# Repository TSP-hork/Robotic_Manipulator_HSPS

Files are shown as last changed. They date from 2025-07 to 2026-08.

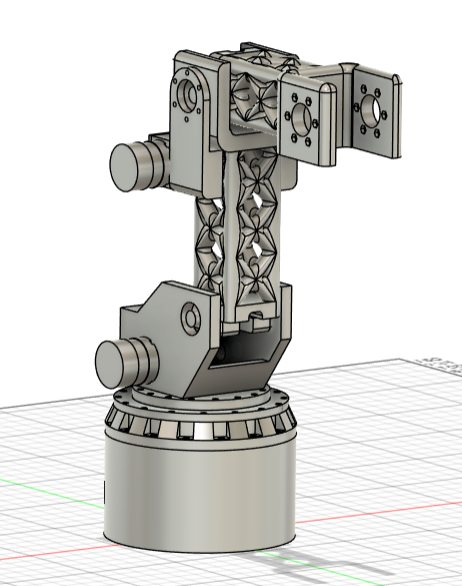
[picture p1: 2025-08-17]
cad/docs/CAD_views/Atlas_v1_pict_3.png

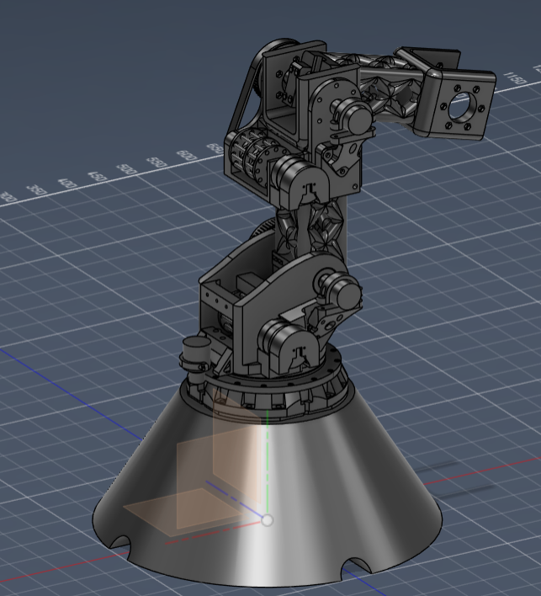
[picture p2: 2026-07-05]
cad/docs/CAD_views/Atlas_v2_pict_1.png

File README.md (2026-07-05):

# Robotic_Manipulator_HSPS

This repository is dedicated to the development of a High-Performance, Open-Source Robotic Manipulator based on a Hot-Swappable Part System (HSPS).

## Hot... what?

Yes, "Hot-Swappable" sounds strange for a robotic arm. Controlling a robot like this usually requires deep programming skills and a complex system understanding, making most designs rigid and hard to modify. My goal is to make it easier. And no, this is not a toy for grabbing cubes.

## What does "not a toy" mean?

A toy can grab something. A toy can rotate. This robot is designed to be a true industrial tool. It's designed to be precise and powerful enough to mill its own parts from aluminum, to weld, or to perform any task you can imagine.

The core idea is simple: This project provides a blueprint for anyone with common tools (like a 3D printer) and dedication to build an instrument capable of creating almost anything.

## How "good" is this cheap thing?

You might be thinking: "Okay, so you're making a cheap little arm and believe it can compete with a true, big, metal one? That's nonsense." And you are half right. This robot can't mill hardened steel or titanium. But does it need to?

What we all really need are strong, precise parts. We can't 3D-print metal, but this robot is designed to be precise enough to **mill aluminum**. This means you can use the first plastic robot to create the parts for its much stronger, metal successor. Sounds more realistic now, doesn't it?

But what about the "brains"? I've got you covered there too. This robot is being designed to run its control loop at **50 kHz**. This means it can react to a command in **20 microseconds** - the time from your signal to a change in the motor's current. And yes, it will work with almost any motor you want.

## Nice to meet you

I bet this sounds interesting. I just want to say hello, and I'm glad to see you here. This project started on May 27, 2025, and my goal is to build the first working prototype by next summer.

Maybe I'll make it, maybe I won't, but we'll find that out together. For now, you can find me here every Saturday. Let's get started!

## 05.07.26 Update "After a year"

Yeah, looking back, I wasn't sure what I was getting into at the start. I honestly thought I'd just tinker for a month and drop it, but here we are. Let's see what we've achieved!

I have finished the mechanics (I'd say they are 99% done). I also developed a 1kW motor driver—you can grab the Gerbers and order the boards for yourself(please note the non-commercial license below! sry for that). I've tested it and it works great, though I will personally be running it at 200W for this robot. I also wrote the FOC algorithm to control the motors.

I'll be continuing this journey, and I might change the name of the project soon. I really was here almost every Saturday (well, maybe not every single one, but I tried!).

A huge thank you to the two guys who starred my repo—it means a lot! I will keep going, we can do this! <Have a good day!> :>

## ⚖️ License

This project uses a **Dual-Licensing** model to protect both the software and the hardware designs.

*   **Software / Firmware:** All source code in this repository is licensed under the **GNU General Public License v3.0 (GPLv3)**. See the `LICENSE` file in the root directory for details.
*   **Hardware Designs:** All hardware files (Gerbers, Schematics, BOM, Pick and Place files, and 3D CAD models) located in the hardware/cad directories are licensed under the **Creative Commons Attribution-NonCommercial 4.0 International (CC BY-NC 4.0)** license. See the `LICENSE_HARDWARE.md` file for details.

**What this means for you:**
You are completely free to use, modify, and build the software and hardware for your own personal, educational, or hobby projects. However, **you may not use the hardware files for commercial purposes** (e.g., you cannot mass-produce the PCBs to sell them) without explicit permission.

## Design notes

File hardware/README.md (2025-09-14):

This document outlines the core hardware architecture and key component decisions for the project.
*If I write it 100 times, I won't forget it ~~(but that might not be true)~~.*

## 2025-08-14: Hardware Architecture Decisions

* **System Architecture:** The core control system will be a **unified motherboard**. This board will house the primary MCandFPGA, and provide standardized **blade ports** for connecting to the external **power stages** and other peripherals.

* **Performance Target:** The architecture is designed with a future performance target of **200+ kHz** for the core control loop, ensuring a high ceiling for future optimizations.

* **Core Philosophy:** A hybrid **MC + FPGA** approach. The microcontroller acts as the "smart" commander for high-level tasks, while the FPGA serves as the "fast and strong" hardware accelerator for real-time control loops.

* **Microcontroller (MC):** STM32H7A3. Chosen for its powerful Cortex-M7 core, large SRAM, and sufficient processing power to handle kinematics and trajectory planning without becoming a bottleneck.

* **FPGA:** Lattice ECP5, LFE5U-45F. This chip is selected for its excellent balance of price and performance. With **44K LUTs**, it has more than enough resources to implement six parallel, **hardware-accelerated FOC cores**, leaving significant potential for future features.

* **power on mainboard** POWER on board going from board with stabilizators, filters and maybe little MC who just watch for safe all board and stop the current if he is very high. And in future i want only 48 V for step down on blades(if that needs) and mother board.

* **power on input board** POWER on this board comming from any POWER supply who can give 300 W +- or any other count of W 

* **Input board** Thats board is not very smart. with simple MC and passive components who stabilize and filter input POWER.
Is step up or step down supply and send it to main board on two wire VCC and GND. Mb in very far future i make uart for errors from this stage but i think one LED is over and enough.

* **outcontrol blade** is technologist in my system, he can be very smart or very ..khm he can be SD and just talking simple commands, or its can be computer with cam with AI who can talk with this world of any protocol, but with arm he talking on speed of electricity (i just like how its sounds).

* **between FPGA and blade** While i dont forgeted, FPGA not strong enough for control blades and he need a help. For this on road from his leg to blade we need dif converter (working on RS-422) who can send his messages without noices to gate driver. This guy can control strong MOSFETs very fast and he is cheap we accept him to our team. 

## 2025-08-24: the architecture of my electronics

* **main date** so today i start develop my electronics, and start print mechanic. I add new directory to docs for top_sheet. i think i need develop electronics parralel work cuz develop electronics need more time for think than act. Have a good last days of summer -^-

## 2025-09-02: Structure update !!

```
hardware/
├── libraries/
│   ├── symbols/
│   │   └── My_Symbols.SchLib
│   ├── footprints/
│   │   └── My_Footprints.PcbLib
│   └── 3d_models/
│       ├── SP3485.step
│       └── LFE5U-45F.step
├── projects/
│   ├── Axis_Channel_Blade/
│   │   ├── Axis_Channel.PrjPcb
│   │   ├── Axis_Channel.SchDoc
│   │   └── Axis_Channel.PcbDoc
│   ├── Motherboard/
│   │   ├── Motherboard.PrjPcb
│   │   ├── ...
│   └── Input_Board/
│       ├── Input_Board.PrjPcb
│       ├── ...
├── production/
│   ├── Axis_Channel_Blade/
│   │   ├── rev1.0/
│   │   │   ├── gerber/
│   │   │   ├── bom/
│   │   │   └── pick_and_place/
│   │   └── rev1.1/
│   │       ├── ...
│   └── Motherboard/
│       └── rev1.0/
│           ├── ...
└── datasheets/
    ├── IC/
    │   ├── LFE5U-45F.pdf
    │   └── SN65HVD75.pdf
    └── connectors/
        └── Samtec_QSE_series.pdf
```

* **start develop POWER blade** With structure i start to develop blade and for today maked arhitecture of blade

## 2025-09-09: for future :>

* **INA190** amplifier for function hot swap motors. we can change V/V using logic signals from stm. Or we can just use better ADC and place low shunt (1 M ohm) for any current ~~(max 50A)~~ but its expensive.

* **Comment** : for version 1.0, I don't do hot swapping because if I don't build this robot or it doesn't work with my motors, it won't work with any motors, and it doesn't make sense anyway :/ 
**But if it works, I'll definitely make this feature the first one.**

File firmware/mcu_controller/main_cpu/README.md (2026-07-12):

# Main CPU Firmware Architecture

## Overview

This firmware runs on the STM32H7 (280 MHz Cortex-M7) and implements the
control algorithms for a robotic manipulator. The architecture is designed
around three principles:

1. **Portability** — algorithms are hardware-independent and can run on any MCU
2. **Extensibility** — new features are added without modifying existing code
3. **Determinism** — zero runtime overhead from the architecture itself

The system is split into layers. Each layer has exactly one responsibility
and exactly one reason to change.

```
┌─────────────────────────────────────────────┐
│  logic/         Pure algorithms (C/C++)     │ ← portable
│  utility/       Reusable building blocks    │ ← portable (planned)
│  abstract/      Hardware contract (C)       │ ← stable, rarely changes
│  driver/        Chip-specific code (C/ASM)  │ ← replaced per platform
└─────────────────────────────────────────────┘
```

The final system will implement a real-time cascade:

```
Trajectory (100 Hz)                             ← logic done (not integrated)
    → Kinematics (100 Hz)                       ← positioner done, wrist skeleton
        → Servo loop (1 kHz)                    ← logic done (not integrated)
            → FOC current loop (20 kHz)         ← IMPLEMENTED
                → PWM output (via FPGA)         ← IMPLEMENTED
```

Each level only talks to its neighbors. FOC does not know about kinematics.
Kinematics does not know about PWM registers.

## Current State

The FOC current control layer is fully operational on hardware. The higher
cascade levels are being built bottom-up as portable, desktop-testable logic:
the servo loop, the trajectory planner, and the 3-axis kinematics positioner
are written and validated but not yet wired into the running cascade. The wrist
(orientation) kinematics, runtime state machine, and safety guardian remain to
be done.

**What works today:**
- Field-Oriented Control with Clarke/Park transforms
- PI current regulators (d-axis and q-axis)
- Space-Vector PWM modulation with min-max injection
- Full-duplex SPI data exchange with the FPGA at 20 kHz
- Multiple compile-time run modes for calibration and testing
- 280 MHz clock configuration (HSE bypass + PLL)
- DMA-driven SPI slave with EXTI interrupt

**Logic written & validated (portable, desktop-tested, not yet integrated):**
- Position/velocity servo loop with feed-forward
- Jerk-limited S-curve trajectory planning + multi-axis interpolator
- Forward kinematics (general, any axis count) + 3-axis closed-form inverse
- Geometric Jacobian and manipulability (singularity) measure
- Software FPU sin/cos provider (swappable backend)

**What is planned:**
- Servo loop compile-time extensions (damping, friction, …)
- Wrist / orientation inverse kinematics (4/5/6-axis, skeleton in place)
- Cascade integration (trajectory → kinematics → servo → FOC)
- State machine and operating modes
- Technologist module communication protocol
- Safety guardian (last barrier before hardware)
- Hardware CORDIC acceleration for sin/cos (needs a CORDIC-equipped MCU)

## Directory Structure

```
main_cpu/
│
├── 1_logic/                            # Pure algorithms — PORTABLE
│   ├── foc.c                           # FOC: Clarke, Park, PI, inv. Park, SVPWM
│   ├── foc.h                           # FOC interface and output structures
│   └── pid.h                           # PI controller (static inline)
│   │
│   ├── 0_foc/                          # (planned) FOC refactored into C++ class
│   │   ├── foc.hpp
│   │   ├── clarke_park.hpp
│   │   └── svpwm.hpp
│   │
│   ├── 1_servo/                        # Position/velocity servo — IMPLEMENTED
│   │   ├── servo.c / .h                # Cascade P-pos + PI-vel, with feed-forward
│   │   └── extensions/                 # (planned) Servo loop extensions (∞)
│   │       ├── damping/
│   │       │   └── damping.hpp
│   │       ├── friction/
│   │       │   └── friction.hpp
│   │       └── .../
│   │
│   ├── 2_kinematics/                   # Forward/inverse kinematics — IMPLEMENTED (logic only)
│   │   ├── kinematics.c / .h           # Façade + core: general FK, IK dispatch, Jacobian
│   │   ├── seg_position3.c / .h        # Closed-form 3-axis positioner (base + shoulder + elbow)
│   │   └── seg_wrist3.c / .h           # (skeleton) 1/2/3-DOF wrist for 4/5/6-axis arms
│   │
│   ├── 3_trajectory/                   # Path planning — IMPLEMENTED (logic only)
│   │   ├── s_curve.c / .h              # Jerk-limited 7-segment S-curve profile
│   │   └── interpolator.c / .h         # Multi-axis sync + waypoint sequencing
│   │
│   ├── 4_runtime/                      # (planned) System orchestration
│   │   ├── state_machine.cpp
│   │   ├── homing.cpp
│   │   ├── protocol/                   # Technologist module communication
│   │   │   ├── packet.cpp
│   │   │   ├── commands.cpp
│   │   │   └── feedback.cpp
│   │   └── modes/                      # Special operating modes (∞)
│   │       └── resonance_scan/
│   │
│   └── safety/                         # (planned) Safety — ALWAYS ON
│       ├── guardian.cpp
│       └── watchdog.cpp
│
├── 2_utility/                                # (planned) Reusable building blocks
│   ├── math/
│   │   ├── matrix/
│   │   ├── quaternion/
│   │   └── spline/
│   ├── control/
│   │   ├── pid/
│   │   └── filters/
│   ├── signal/
│   │   └── dsp/
│   └── utils/
│       ├── ring_buffer/
│       └── crc/
│
├── 3_abstract/                         # Hardware contract — STABLE
│   └── types.h                         # Shared structures (SPI packets, phase_t)
│   └── hw_contract.h                   # (planned) Documents required HW functions
│
├── 4_driver/stm32h7a3zit6_Q/          # Chip-specific — REPLACEABLE
│   ├── config.h                        # Run mode, motor params, ADC calibration
│   ├── hw_impl.h                       # Inline HW functions (the bridge)
│   ├── hw_binding.c                    # Peripheral init orchestration
│   ├── isr.c                           # EXTI4 handler (FOC pipeline runs here)
│   ├── spi.c                           # SPI3 slave + DMA configuration
│   ├── spi.h
│   ├── rcc.c                           # Clock tree (280 MHz from HSE + PLL)
│   ├── rcc.h
│   ├── gpio.c                          # Diagnostic LED pins
│   ├── gpio.h
│   ├── tim.c                           # TIM6 microsecond timer
│   ├── tim.h
│   └── startup/
│       ├── STM32H7A3ZITXQ_FLASH.ld    # Linker script
│       └── startup_stm32h7a3xx.s       # Vector table + reset handler
│
├── tests/                              # Desktop unit tests (NOT built into firmware)
│   └── test_trajectory.c               # Host-compiled tests for 3_trajectory/
├── main.cpp                            # Entry point + configuration
├── CMakeLists.txt                      # Build system (ARM cross-compilation)
└── Makefile                            # Convenience wrapper (config/build/flash)
```

Items marked **(planned)** do not exist yet. They represent the target
architecture that will be built incrementally.

---

## Layer Rules

### logic/ — Pure Algorithms

**Language:** C today, C++ when servo layer is added

**Rules:**
- NEVER includes chip-specific headers directly
- NEVER accesses hardware registers
- ONLY calls functions from `hw_impl.h` and `utility/`
- CAN be compiled and tested on a desktop PC

**Numbering convention:** prefixes `0_`, `1_`, `2_`, `3_`, `4_` indicate the
cascade level. Lower number = faster loop = closer to hardware.

```
0_foc        20 kHz    current control          ← IMPLEMENTED (as foc.c)
1_servo       1 kHz    position/velocity        ← logic done, not integrated
2_kinematics  100 Hz   joint-to-cartesian       ← positioner done, wrist skeleton
3_trajectory  100 Hz   path planning            ← logic done, not integrated
4_runtime     main()   state machine, commands  ← planned
```

### utility/ — Reusable Building Blocks (planned)

**Language:** C or C++

**Rules:**
- Pure math and utilities — no hardware, no state machines
- Each block is self-contained with its own `.h` and `.c`/`.cpp`
- ONLY placed in `utility/` if used by **more than one** module in `logic/`
- If used by only one module — keep it inside that module

**Grouping:**
- `math/` — linear algebra, quaternions, splines
- `control/` — PID, filters, observers
- `signal/` — DSP, FFT, spectral analysis
- `utils/` — ring buffers, CRC, data structures

### abstract/ — Hardware Contract

**Language:** C (with `extern "C"` guards)

**Rules:**
- Contains ONLY header files
- `types.h` defines shared data structures used across all layers
- `hw_contract.h` (planned) documents the functions that `driver/` must implement
- This layer **almost never changes** — it is the stable interface

**Currently implemented:** `types.h` with SPI packet structures (`spi_rx_packet_t`,
`spi_tx_packet_t`, `axis_rx_t`, `axis_tx_t`), FOC types (`phase_t`, `rotor_t`),
and compile-time size assertions.

**`hw_contract.h` will document** the functions that every `driver/xxx/hw_impl.h`
must provide:

```
// hw_contract.h — Every driver/ MUST provide hw_impl.h containing:
//
//   static inline phase_t  hw_read_currents(void);
//   static inline rotor_t  hw_read_rotor(void);
//   static inline void     hw_write_pwm(phase_t duty);
//   static inline void     hw_sincos(float angle, float *s, float *c);
//   static inline void     hw_enable_gate(void);
//   static inline void     hw_disable_gate(void);
//   static inline uint32_t hw_micros(void);
```

### driver/ — Chip-Specific Implementation

**Language:** C + ASM

**Rules:**
- ONLY this layer knows about registers, DMA channels, pin numbers
- Implements all functions listed in `hw_contract.h`
- `hw_impl.h` uses `static inline` — zero overhead, compiler inlines everything
- `vendor/CMSIS/` contains third-party headers — **do not edit**
- When switching MCU, **only this layer is rewritten**

**Currently implemented:**
- `rcc.c` — full clock tree (280 MHz: HSE bypass → PLL → SYSCLK)
- `gpio.c` — diagnostic LED pins (PB0, PE1, PB14)
- `tim.c` — TIM6 as 1 µs free-running timer
- `spi.c` — SPI3 slave with DMA + EXTI4 interrupt on CS line
- `isr.c` — EXTI4 handler running the entire FOC pipeline
- `hw_binding.c` — calls all peripheral inits in correct order
- `hw_impl.h` — SPI buffer accessors (full hw functions are stubs for now)
- `config.h` — motor parameters, run mode selection, calibration constants

---

## How It Works Today

### The Interrupt-Driven FOC Loop

The entire control loop is driven by a single interrupt — EXTI4 on PA4,
triggered by the FPGA's SPI chip-select signal at 20 kHz:

```
FPGA asserts CS (falling edge)
    │
    ▼
EXTI4 ISR: configure DMA, enable SPI3
    │
    ... 256-bit SPI transfer (hardware, no CPU) ...
    │
FPGA releases CS (rising edge)
    │
    ▼
EXTI4 ISR: disable SPI3, then:
    1. Read RX buffer (encoder positions + ADC currents from FPGA)
    2. Run FOC: Clarke → Park → PI → inverse Park → SVPWM
    3. Fill TX buffer (PWM duty commands for FPGA)
    4. Reset SPI3 peripheral for next frame
    5. Return from ISR
    │
    ▼
CPU sleeps (__WFI) until next CS edge
```

No timer interrupts. No polling loops. The FPGA's 20 kHz tick is the sole
timing reference for the MCU.

### SPI Data Exchange

The MCU communicates with the FPGA via a 256-bit (32-byte) full-duplex
SPI frame every 50 µs. Packet structures are defined in `types.h`:

**FPGA → MCU (sensor data):**
```
typedef struct __attribute__((packed)) {
    uint32_t  sync;                     // 0xAA55AA55 — frame validation
    axis_rx_t axis[AXIS_COUNT];         // Per-axis: 2×16-bit ADC + 32-bit encoder
    uint32_t  sequence;                 // FPGA frame counter
} spi_rx_packet_t;
```

**MCU → FPGA (commands):**
```
typedef struct __attribute__((packed)) {
    uint32_t  magic;                    // 0xDEADBEEF — link validation
    axis_tx_t axis[AXIS_COUNT];         // Per-axis: 3×16-bit PWM + 16-bit flags
    uint32_t  status;                   // MCU processed-frame counter
} spi_tx_packet_t;
```

Both packets are exactly 32 bytes. Compile-time `_Static_assert` checks
guarantee size consistency.

### Run Modes

Operating behavior is selected at compile time via `RUN_MODE` in `config.h`.
This avoids runtime branching overhead and allows the compiler to eliminate
dead code entirely.

| Mode | Name | Description |
|---|---|---|
| 0 | Open-loop rotation | Rotating voltage vector, no feedback. ADC test |
| 1 | Encoder test | Motor disabled, encoder readback only |
| 2 | Alignment | Static d-axis vector, captures encoder offset  |
| 3 | Align → FOC | 2s alignment, then closed-loop current control |
| 4 | Full FOC | All axes, production mode (needs outer loop) |

### FOC Pipeline (foc.c)

Executes every 50 µs inside the EXTI4 ISR:

```
Phase currents (ia, ib from FPGA's ADC data)
        │
        ▼
  Clarke Transform
  ia, ib → iα, iβ
        │
        ▼
  Park Transform (using electrical angle from encoder)
  iα, iβ → id, iq
        │
        ▼
  PI Current Regulators (pid.h, static inline)
  id_error → vd    (flux, always targets 0)
  iq_error → vq    (torque, set by outer loop or test constant)
        │
        ▼
  Inverse Park Transform
  vd, vq → vα, vβ
        │
        ▼
  SVPWM Modulator (min-max injection, +15% bus utilization)
  vα, vβ → pwm_a, pwm_b, pwm_c  (0..PWM_PERIOD ticks)
        │
        ▼
  Packed into SPI TX buffer → sent to FPGA on next frame
```

### The Bridge: hw_impl.h

This file connects portable logic to real hardware. Currently it provides
SPI buffer accessors. As the architecture matures, it will contain direct
register access for ADC, PWM, and CORDIC:

```
// Current state: SPI-mediated access to FPGA buffers
static inline volatile spi_rx_packet_t* hw_spi_rx_buf(void) {
    return spi_get_rx();
}

// Future state: direct hardware access (zero overhead)
static inline phase_t hw_read_currents(void) {
    return (phase_t){
        .a = (float)adc_buf[0] * CURRENT_SCALE,
        .b = (float)adc_buf[1] * CURRENT_SCALE,
        .c = (float)adc_buf[2] * CURRENT_SCALE,
    };
}
```

Logic calls `hw_read_currents()`. At compile time, the compiler replaces this
with direct register access. **Zero function call overhead.**

### main.cpp — Entry Point

```
int main(void) {
    SCB->VTOR = 0x08000000;    // Vector table in Flash
    hw_binding_init();          // RCC → GPIO → TIM6 → SPI3+DMA+EXTI
    foc_init();                 // Zero PI integrators, set gains
    __enable_irq();             // EXTI4 starts firing at 20 kHz

    while (1) {
        __WFI();                // Sleep until next interrupt
    }
}
```

**main.cpp is the configuration file.** When the servo layer is added, it
will also define the extension pipeline:

```
// Future main.cpp
auto servo_chain = ServoChain{
    Damping{.freq = 45.0f, .gain = 0.3f},
    FrictionComp{.coulomb = 0.1f},
};
```

---

## Configuration

All tunable parameters are in `4_driver/stm32h7a3zit6_Q/config.h`:

```
#define RUN_MODE         3          // Operating mode (0–4)
#define AXIS_COUNT       3          // Number of motor axes
#define PWM_PERIOD       1350       // PWM counter ceiling (matches FPGA)
#define POLE_PAIRS       2          // Motor pole pairs
#define ENCODER_CPR      2048       // Encoder counts per revolution (X4)
#define CURRENT_SCALE    0.5f       // ADC counts → amperes
#define CURRENT_OFFSET   2048       // ADC zero-current midpoint (12-bit mid-scale)
#define TEST_IQ_REF      0.12f      // Test torque reference (amps)
#define ALIGN_TIME       3000       // Alignment duration (packets ≈ 150 ms)
#define ALIGN_AMPLITUDE  0.16f      // Alignment voltage (normalized 0..1)
```

---

## Clock Tree

```
HSE (8 MHz external bypass oscillator)
    │
    ▼
PLL1: 8 / 1 × 70 = 560 MHz VCO
    │
    ├── / 2 → SYSCLK = 280 MHz  (CPU core)
    ├── / 1 → AHB    = 280 MHz  (DMA, GPIO)
    ├── / 2 → APB1   = 140 MHz  (SPI3, TIM6)
    └── / 2 → APB2   = 140 MHz

Power: SMPS mode, VOS0 voltage scaling (required for > 225 MHz)
Flash: 6 wait states (required for 280 MHz)
```

---

## Safety Architecture (planned)

Guardian will sit between extensions and hardware output. It catches any
invalid value before it reaches the motor:

```
Extensions (may have bugs)
        │
        ▼
╔═══════════════════╗
║  GUARDIAN          ║  NaN? → STOP
║                   ║  Over limit? → STOP
║                   ║  Watchdog? → STOP
╚════════╤══════════╝
         ▼
    FOC output
         ▼
    HW comparator (last resort, hardware-level)
```

Guardian will be **never disabled.** There will be no `#if FEATURE_SAFETY`.

Three independent safety layers (planned):
1. `safety/guardian` — software checks (NaN, limits, watchdog)
2. FOC overcurrent — software current limit inside PI regulators
3. Hardware comparator — analog, works even if CPU hangs

---

## How to Extend

### Adding a Servo Loop Extension (future)

**You need to know:**
1. Create a struct with a `step()` method
2. Add one line in `main.cpp`

**You do NOT need to know:**
- How FOC works
- What MCU is used
- How interrupts are configured
- How the pipeline works internally

**Step 1:** Create your extension

```
logic/1_servo/extensions/my_feature/
└── my_feature.hpp
```

```
struct MyFeature {
    float my_param;

    float step(float torque, Axis& axis) {
        return torque + my_param * axis.velocity;
    }
};
```

**Step 2:** Add to main.cpp

```
auto servo_chain = ServoChain{
    Damping{.freq = 45.0f, .gain = 0.3f},
    MyFeature{.my_param = 0.5f},             // ← this line
};
```

**Step 3:** Build. Done.

The compiler inlines your `step()` into the servo loop. Zero overhead.
No function pointers. No vtables. As fast as if you wrote it by hand.

### Adding a New Run Mode (today)

1. Add a new `#elif RUN_MODE == N` block in `isr.c`
2. Define any new constants in `config.h`
3. Set `RUN_MODE` to your new value in `config.h`
4. Build and flash

### Adding a New Hardware Sensor

**Step 1:** Add inline reader to `driver/hw_impl.h`

```
static inline float hw_read_new_sensor(void) {
    return (float)SOME_REGISTER * SCALE;
}
```

**Step 2:** Document in `abstract/hw_contract.h`

```
//   static inline float hw_read_new_sensor(void);
```

**Step 3:** Use from `logic/` — done

```
float val = hw_read_new_sensor();  // zero overhead, inlined
```

### Adding a New Library Block (future)

```
2_utility/control/my_filter/
├── my_filter.h
└── my_filter.c
```

**Rule:** only move to `2_utility/` if used by more than one module in `logic/`.
Otherwise keep it inside the module that uses it.

---

## How to Port to a New MCU

1. Create new `4_driver/new_mcu/` directory
2. Implement every function listed in `abstract/hw_contract.h`
3. Write startup, ISR, and peripheral init for the new chip
4. Update `CMakeLists.txt` to point to the new driver directory
5. **Do not touch `1_logic/` or `3_abstract/`**

```
What changes:           4_driver/   (rewrite)
                        main.cpp    (adjust init if needed)
                        CMakeLists  (point to new driver)

What stays identical:   1_logic/    (all algorithms)
                        2_utility/        (all building blocks)
                        3_abstract/ (the contract)
```

---

## Build & Flash

```
# Full cycle: configure + build + flash
make all

# Step by step:
make config              # CMake configure (Release by default)
make config TYPE=Debug   # CMake configure (Debug, -O0 -g3)
make build               # Compile
make flash               # Program via ST-Link + OpenOCD

# Clean
make clean
```

**Requirements:**
- `arm-none-eabi-gcc` (13.x or later)
- `cmake` (3.20+)
- `openocd` (0.12+)
- ST-Link V2/V3 debug probe

---

## Implementation Status

| Feature | Status | Location |
|---|---|---|
| FOC current control | ✅ Working | `1_logic/foc.c` |
| SVPWM modulation | ✅ Working | `1_logic/foc.c` |
| PI current regulators | ✅ Working | `1_logic/pid.h` |
| SPI slave (DMA + EXTI) | ✅ Working | `4_driver/spi.c` |
| Clock tree (280 MHz) | ✅ Working | `4_driver/rcc.c` |
| Run modes 0–4 | ✅ Working | `4_driver/isr.c` |
| Alignment calibration | ✅ Working | `4_driver/isr.c` |
| SPI packet structures | ✅ Working | `3_abstract/types.h`  |
| hw_impl.h (SPI access) | ✅ Working | `4_driver/hw_impl.h`  |
| hw_impl.h (direct HW) | 🔲 Stub | `4_driver/hw_impl.h` |
| hw_contract.h | ✅ Working | `3_abstract/` |
| Position servo loop | ✅ Working | `1_servo/servo.c` |
| Velocity control | ✅ Working | `1_servo/servo.c` |
| Servo→FOC integration | 🔲 Planned  | (caller wires it) |
| Servo extensions | 🔲 Planned  | `1_servo/extensions/`  |
| hw_sincos (software FPU) | ✅ Working | `4_driver/.../sincos/` |
| Safety guardian | 🔲 Planned  | `safety/` |
| Forward kinematics (DH)  | ✅ Working | `2_kinematics/kinematics.c` |
| Inverse kin. (3-axis) | ✅ Working | `2_kinematics/seg_position3.c`|
| Jacobian + manipulability| ✅ Working | `2_kinematics/kinematics.c` |
| Wrist / orientation IK | 🔲 Skeleton | `2_kinematics/seg_wrist3.c` |
| Kinematics (servo hookup)| 🔲 Planned  | (caller wires it) |
| Jerk-limited S-curve | ✅ Working | `3_trajectory/s_curve.c` |
| Multi-axis interpolator  | ✅ Working | `3_trajectory/interpolator.c`|
| Trajectory (servo hookup)| 🔲 Planned  | `1_servo/` (consumer)  |
| State machine | 🔲 Planned  | `4_runtime/` |
| Technologist protocol | 🔲 Planned  | `4_runtime/protocol/`  |
| Hardware CORDIC | 🔲 Planned  | `4_driver/` |
| Library blocks | 🔲 Planned  | `2_utility/` |
| Desktop unit testing | ✅ Working | `tests/` |

---

## Language Policy

| Layer | Language | Why |
|---|---|---|
| `1_logic/` | C (→ C++) | Portable today; C++ when servo chain is added |
| `2_utility/` | C or C++ | Pure math, maximum compatibility |
| `3_abstract/`| C | Must be visible from both C and C++ |
| `4_driver/`  | C + ASM | Direct register access, CMSIS compatibility |
| `main.cpp` | C++ | Future: C++ servo chain configuration |

C++ features planned: `templates`, `constexpr`, `inline namespaces`,
`designated initializers`. No dynamic allocation. No exceptions. No RTTI.

---

## Architecture Diagram

```
main.cpp          ──────────────────────────────────┐
  │ init + config                                   │
  ▼                                                 │
logic/4_runtime/  ◄── protocol/ (technologist)      │  ← planned
  │ commands                                        │
  ▼                                                 │
logic/3_trajectory/                                 │  ← logic done
  │ waypoints                                       │
  ▼                                                 │
logic/2_kinematics/                                 │  ← positioner done
  │ joint angles                                    │
  ▼                                                 │
logic/1_servo/    ◄── extensions/ (compile-time)    │  ← logic done
  │ torque         │                                │
  │                ▼                                │
  │            safety/guardian  ← ALWAYS ON          │  ← planned
  │                │                                │
  ▼                ▼                                │
logic/0_foc/  (foc.c + pid.h)                       │  ← IMPLEMENTED
  │ PWM duty                                        │
  ▼                                                 │
abstract/types.h  ◄──────── driver/hw_impl.h ───────┘  ← IMPLEMENTED
  │                             │
  ▼                             ▼
EXTI4 ISR (isr.c)          SPI3 + DMA (spi.c)         ← IMPLEMENTED
  │                             │
  ▼                             ▼
SPI packets ◄──────────────► FPGA (external)
```

---

## FAQ

**Q: Where do I put a new algorithm?**
A: If it modifies the servo torque → `logic/1_servo/extensions/`.
If it is a new operating mode → `logic/4_runtime/modes/`.
If it is reusable math → `2_utility/`.
If it is a new run mode today → `#elif` block in `isr.c`.

**Q: Can I write my extension in pure C?**
A: Yes. Write a C function and call it from your C++ `step()` method.
The struct wrapper is minimal — one method, one line.

**Q: What if I need data from a sensor that hw_impl.h doesn't expose?**
A: Add a `static inline` function to `driver/hw_impl.h`, document it in
`abstract/hw_contract.h`. Then call it from `logic/`.

**Q: How do I disable a feature?**
A: Remove its line from `servo_chain` in `main.cpp`. The compiler will
eliminate all dead code. Zero bytes in the binary.

**Q: Why is FOC in a .c file instead of a C++ class?**
A: The current implementation prioritizes getting the motor spinning.
Once the servo layer is added, FOC will be refactored into `0_foc/foc.hpp`
as a C++ class to match the extension architecture.

**Q: Why does the MCU sleep in main() instead of running a loop?**
A: All real-time work happens inside EXTI4_IRQHandler, triggered by the
FPGA at exactly 20 kHz. Between interrupts there is nothing to do — `__WFI`
saves power and guarantees deterministic interrupt entry latency.

**Q: Why not use virtual functions / function pointers for extensions?**
A: The servo loop will run at 1 kHz. Each indirect call costs 3-5 clock
cycles. With many extensions that adds up. C++ templates resolve everything
at compile time — zero overhead, as fast as hand-written code.

**Q: What guarantees safety today?**
A: Currently only the PI output limiter (±1.0 normalized) and PWM clamping
(0..PWM_PERIOD) in SVPWM. The full three-layer safety system (guardian +
software overcurrent + hardware comparator) is planned.
```

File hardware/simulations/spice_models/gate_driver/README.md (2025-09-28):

**comment**
**28.09.25** : We will use spice model from TI for similar MOSFET cuz they have same characteristics

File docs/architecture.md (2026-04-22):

## Architecture.md

# Architecture of the HSPS Robotic Manipulator

## Table of Contents

- [1. Overview](#1-overview)
- [2. Core Concept](#2-core-concept)
- [3. System Architecture](#3-system-architecture)
  - [3.1 System Block Diagram](#31-system-block-diagram)
  - [3.2 Data Flow: Control Loop](#32-data-flow-control-loop)
  - [3.3 Power Distribution](#33-power-distribution)
- [4. Electronics Architecture](#4-electronics-architecture)
  - [4.1 Motherboard](#41-motherboard)
  - [4.2 MCU: STM32H7A3](#42-mcu-stm32h7a3)
  - [4.3 FPGA: Lattice ECP5 (LFE5U-45F)](#43-fpga-lattice-ecp5-lfe5u-45f)
  - [4.4 MCU ↔ FPGA Communication](#44-mcu--fpga-communication)
  - [4.5 Power Blade (Axis Channel)](#45-power-blade-axis-channel)
  - [4.6 Technologist Module](#46-technologist-module)
  - [4.7 Input Power Board](#47-input-power-board)
- [5. Firmware Architecture](#5-firmware-architecture)
  - [5.1 FPGA Modules](#51-fpga-modules)
  - [5.2 MCU Firmware](#52-mcu-firmware)
  - [5.3 Control Loop Timing](#53-control-loop-timing)
- [6. Mechanical Architecture](#6-mechanical-architecture)
  - [6.1 Kinematic Configuration](#61-kinematic-configuration)
  - [6.2 Slew Drive (Rotary Support)](#62-slew-drive-rotary-support)
  - [6.3 Cabin](#63-cabin)
  - [6.4 Shoulder Module](#64-shoulder-module)
  - [6.5 Backpack (Motor + Reducer Mount)](#65-backpack-motor--reducer-mount)
  - [6.6 Balanced Cycloidal Reducer](#66-balanced-cycloidal-reducer)
  - [6.7 Base](#67-base)
- [7. The Technologist Module: Design Philosophy](#7-the-technologist-module-design-philosophy)
- [8. Design Principles](#8-design-principles)
- [9. Target Specifications](#9-target-specifications)
- [10. Current Status and Roadmap](#10-current-status-and-roadmap)

---

## 1. Overview

The HSPS (Hot-Swappable Part System) Robotic Manipulator is a fast, precise,
and affordable robotic arm designed for simple assembly, easy operation,
and tool-agnostic deployment. It is built from four electronic subsystems:
an Input Power Board, a Motherboard, hot-swappable Power Blades, and a
hot-swappable Technologist Module.

The robot is designed so that any person with a 3D printer and basic tools
can build an instrument capable of precise spatial positioning — precise
enough to mill aluminum and manufacture parts for a stronger, metal version
of itself.

## 2. Core Concept

The central idea behind HSPS is the separation of concerns:

- **The Robot** is a precision positioning tool. It moves a point in space
  from A to B. It is a black box with a simple API.
- **The Technologist Module** defines *what to do*. It controls the tool,
  sends high-level commands, and can be swapped in seconds.
- **The Power Blades** drive the motors. They are hot-swappable cards that
  plug into the motherboard via a standard PCIe physical connector.

This separation means that switching from milling to welding requires only
swapping the Technologist Module and the tool — not reprogramming the robot.

## 3. System Architecture

### 3.1 System Block Diagram

```
[PSU 8-60V] ──→ [Input Power Board*] ──→ [MOTHERBOARD]
                                              │
                 ┌────────────┬───────────────┼───────────────┬────────────┐
                 │            │               │               │            │
            [Blade 1]   [Blade 2]   ...  [Blade 6]   [Technologist Module]
                 │            │               │               │
           [Motor+Enc]  [Motor+Enc]     [Motor+Enc]      [Tool/End Effector]

Inside the Motherboard:
┌─────────────────────────────────────────────────────────────────────┐
│                                                                     │
│   [FPGA: Lattice ECP5] ←── data bus ──→ [MCU: STM32H7A3]          │
│        │                                      │                     │
│        ├─ PWM signals      → Blade PCIe slots  ├─ FOC algorithm     │
│        ├─ Encoder data     ← Blade PCIe slots  ├─ Inverse kinematics│
│        ├─ SPI (ADC data)   ← Blade PCIe slots  ├─ API ↔ Tech Module│
│        ├─ Hardware dead-time protection         ├─ State machine     │
│        └─ Hardware clock sync (for clustering)  └─ Trajectory plan  │
│                                                                     │
│   [PCIe x8 Slots × 6]              [PCIe Slot × 1: Tech Module]   │
│                                                                     │
└─────────────────────────────────────────────────────────────────────┘

* Input Power Board is not implemented in the prototype.
  The prototype is powered directly from a 24V PSU.
```

### 3.2 Data Flow: Control Loop

Every control cycle (target: 20 µs / 50 kHz):

```
Step 1: FPGA triggers ADC conversion on the Blade
            │
Step 2: STM32G431 (on Blade) samples 3 phase currents
            │
Step 3: ADC data is sent via SPI to the FPGA          ← ~400 ns
            │
Step 4: FPGA decodes quadrature encoders (parallel)   ← 1-2 clock cycles
            │
Step 5: FPGA writes currents + positions directly
        into MCU registers (via data bus)              ← no CPU overhead
            │
Step 6: MCU (STM32H7) executes:
        - Clarke/Park transforms
        - PID current regulators (FOC)
        - Inverse kinematics
        - Trajectory interpolation
            │
Step 7: MCU writes PWM duty cycles directly
        into FPGA registers (via data bus)             ← no CPU overhead
            │
Step 8: FPGA generates 6 PWM signals with
        hardware dead-time insertion
            │
Step 9: PWM signals reach gate drivers on the Blade
            │
Step 10: Motor responds. Cycle repeats.
```

Key architectural advantage: Steps 3, 4, 5, and 7 happen with **zero CPU
involvement**. The FPGA handles all signal acquisition, decoding, and
routing in parallel, while the MCU focuses purely on math. Adding more
sensors or encoders does not increase MCU load or introduce jitter.

> **Current prototype status:** The full control chain has been validated
> at 20 kHz using development boards (Tang Nano 9K as FPGA, STM32H7 Nucleo
> as MCU) connected via SPI. The FPGA acts as SPI master and triggers the
> MCU via EXTI interrupt on each frame. The target architecture (direct
> register bus, 50 kHz) will be implemented on the motherboard.

### 3.3 Power Distribution

```
[External PSU: 8-60V DC]
        │
[Input Power Board*] ── filtering, protection, regulation
        │
[Motherboard Power Rail]
        ├──→ Blade slots (Vbus passthrough to motor drivers)
        ├──→ 12V DC/DC → FPGA, gate driver logic supply
        ├──→ 5V  DC/DC → MCU, digital logic
        ├──→ 3.3V LDO  → MCU core, FPGA I/O banks
        └──→ Technologist Module slot (5V or 3.3V selectable)

Each Blade has its own on-board power regulation:
[Vbus from Motherboard]
        ├──→ 12V DC/DC (TPS54360B) → gate driver bootstrap
        ├──→ 5V  LDO  (LM7805)    → STM32G431, RS-485
        └──→ 3.3V LDO (TLV1117)   → logic, analog reference

* Not implemented in prototype. Robot is powered directly at 24V.
```

---

## 4. Electronics Architecture

### 4.1 Motherboard

The Motherboard is the central hub. It hosts:

- **MCU:** STM32H7A3 — the brain of the robot.
- **FPGA:** Lattice ECP5 (LFE5U-45F) — the signal engine.
- **PCIe x8 slots** (×6) for Power Blades.
- **PCIe x8 slot** (×1) for the Technologist Module.
- **Power input terminals** from the Input Power Board (or directly from PSU).
- **Clock synchronization output** on the Technologist Module connector.

> **Important:** The PCIe x8 connector (98-pin, part: 10018784-10202TLF) is
> used **only as a physical/mechanical connector**. The PCIe protocol is
> **not** used. The pinout is custom-defined for this project.

### 4.2 MCU: STM32H7A3

The MCU is the high-level computational center. Its responsibilities:

- **FOC (Field-Oriented Control)** — Clarke/Park transforms, PID regulators.
- **Inverse kinematics** — converting Cartesian coordinates to joint angles.
- **Technologist Module API** — receiving high-level commands (e.g., "move to
  point X,Y,Z") and decomposing them into per-axis motor control tasks.
- **Trajectory planning** — interpolation, acceleration profiles.
- **System state machine** — initialization, calibration, operation, error
  handling.

The MCU does **not** directly read encoders or generate PWM. All signal I/O
is handled by the FPGA and mapped into MCU memory via the data bus.

### 4.3 FPGA: Lattice ECP5 (LFE5U-45F)

The FPGA is the real-time signal engine. Its responsibilities:

- **PWM generation** — center-aligned PWM at the duty cycle specified by
  the MCU. All channels are generated in parallel.
- **Hardware dead-time insertion** — prevents shoot-through on half-bridges.
  This is a critical safety function implemented in hardware, not software.
- **Quadrature encoder decoding** — reads and decodes encoder signals for
  all axes simultaneously, in parallel, with glitch filtering.
- **ADC data reception** — receives SPI data from the STM32G431 ADC on each
  Blade and places it directly into MCU-accessible registers.
- **Hardware clock synchronization** — generates a synchronization clock
  signal for multi-robot clustering. This clock is routed to the
  Technologist Module connector.

The FPGA communicates with the MCU via a direct data bus that allows
register-level read/write access in both directions.

### 4.4 MCU ↔ FPGA Communication

The MCU and FPGA are connected via a parallel data bus that enables direct
register access:

- The **MCU writes** PWM duty cycles and frequencies directly into FPGA
  registers. No serialization, no protocol overhead.
- The **FPGA writes** encoder positions and ADC values directly into
  MCU-accessible memory. No interrupt handling, no polling.

This architecture eliminates the communication bottleneck that typically
limits multi-axis servo systems. Adding a new axis (a new Blade with
motor and encoders) does not increase the MCU's I/O workload — it only
adds more math to compute.

> The specific bus interface (FMC, FSMC, or custom parallel bus) will be
> finalized during motherboard development.

### 4.5 Power Blade (Axis Channel)

The Power Blade is a modular motor driver on a PCB with a PCIe x8 edge
connector. Each Blade drives one motor (one axis).

**Specifications:**

| Parameter | Value |
|---|---|
| Connector | PCIe x8 (98-pin, physical only) |
| Rated power | 150–300 W (continuous) |
| Peak power (by design) | 1200 W |
| Switching frequency | 50 kHz |
| MOSFETs | NTMFS3D5N08XT1G (80V, 3mΩ, 23nC)  |
| Gate drivers | IRS21867S (4A peak, 600V) |
| Current sensing | INA240A1DR (×3, 20 V/V gain) |
| Shunt resistors | 5mΩ, 3W, 1% |
| On-board ADC | STM32G431RBT6 |
| Communication to FPGA | RS-485 (SN65HVD75DR), SPI |

**Why STM32G431 as ADC?**

A dedicated ADC IC would be cheaper per channel but would require more
external circuitry. The STM32G431 provides three 12-bit ADCs with hardware
synchronization, all in a single $1.5 package. It also runs at 170 MHz,
which allows it to handle the ADC-to-SPI pipeline with a latency of
approximately 400 ns and zero CPU intervention on the main MCU. In the
future, the G431 will also monitor Blade health (temperature, voltage,
fault conditions).

**Thermal note:** At the nominal operating point (24V, 4A), total
conduction losses across all 6 MOSFETs are under 0.3W. Even at the
maximum design current (10A), losses remain under 3W. The SuperSO8
package dissipates this without a heatsink. Active cooling is not required.

> Full component list and selection rationale: see `hardware/docs/components.md`

### 4.6 Technologist Module

The Technologist Module is the user-facing control interface. It plugs into
a dedicated PCIe slot on the Motherboard and communicates with the MCU via
a minimal interface:

```
Pin allocation (conceptual):
- Power:  VCC (5V or 3.3V)
- Ground: GND
- Data:   TX (commands from module → MCU)
- Data:   RX (feedback from MCU → module)
- Clock:  SYNC (hardware synchronization clock from FPGA)

```

From the Technologist Module's perspective, the entire robot is a **black box** with a simple API:

- Send: `MOVE_TO(x, y, z, speed)`
- Send: `SET_JOINT(axis, angle)`
- Receive: `POSITION(x, y, z)`
- Receive: `STATUS(state, error_code)`

The Technologist Module has **no access** to the internal control loop,
FOC parameters, or motor-level commands. It cannot modify the closed-loop
control algorithms.

The module is also directly connected to the end-effector (tool). It
controls the tool independently of the robot's positioning system.

**Key design intent:** Swapping the Technologist Module changes the robot's
task. A milling module commands precise paths and controls a spindle.
A welding module commands different paths and controls a welder. The robot
itself does not change. This is the "hot-swap" in HSPS.

> The physical communication protocol (UART, SPI, or custom) and the
> command format will be finalized during Technologist Module development.

### 4.7 Input Power Board

The Input Power Board sits between the external power supply and the
Motherboard. Its purpose is to protect and condition the incoming power:

- Input voltage filtering (EMI suppression)
- Overvoltage and overcurrent protection (disconnect on fault)
- Voltage regulation/stabilization for noisy or unstable sources
- Accepted input range: 8V to 60V DC

> **Not implemented in the prototype.** The prototype connects a regulated
> 24V PSU directly to the Motherboard. The Input Power Board will be
> developed for the production version after the core concept is validated.

---

## 5. Firmware Architecture

### 5.1 FPGA Modules

The FPGA design is written in SystemVerilog and consists of independent,
parallel modules:

| Module | Function |
|---|---|
| `system_storage` | Central register file (CSR). Shared memory between  |
| | FPGA and MCU for all axis data. |
| `pwm_generator` | Center-aligned PWM generation for FOC. |
| `deadtime` | Hardware dead-time insertion. Prevents shoot-through|
| | on half-bridge MOSFETs. Cannot be bypassed by SW.  |
| `quadrature_decoder`  | Decodes ABZ encoder signals with glitch filtering. |
| `spi_master` | Configurable-width SPI master for MCU and ADC |
| | communication. |
| `top` | Top-level integration: 3-axis instantiation, |
| | exchange FSM, tick timer. |

All modules run in parallel. Adding a new axis means instantiating another
set of modules — no impact on existing axes' timing.

### 5.2 MCU Firmware

> **Status:** The FOC algorithm is implemented and validated at 20 kHz on
> development boards (Tang Nano 9K + STM32H7 Nucleo). The target frequency
> of 50 kHz will be achieved on the final motherboard with FMC bus.

The MCU firmware runs on the STM32H7A3 and implements:

- **FOC (Field-Oriented Control):** Clarke/Park transforms, PI current
  regulators in the d-q reference frame. **Implemented and tested.**
- **SVPWM modulation:** Space-vector PWM with min-max injection for
  optimal DC bus utilization. **Implemented and tested.**
- **Position/velocity control loop:** Outer loop using encoder feedback.
  *Planned.*
- **Inverse kinematics solver:** Converts Cartesian commands from the
  Technologist Module into joint-space targets. *Planned.*
- **Technologist Module communication handler:** Parses incoming commands,
  queues them (FIFO), executes in order, sends back position feedback.
  *Planned.*
- **State machine:** Manages robot states (boot → calibration → idle →
  moving → error → emergency stop). *Planned.*

### 5.3 Control Loop Timing

Target control loop period: **20 µs (50 kHz)**.

```
Budget breakdown (target):

ADC sampling + SPI transfer:     ~0.5 µs
FPGA encoder decoding:           ~0.02 µs (1-2 FPGA clock cycles)
FPGA → MCU register write:       ~0.1 µs
MCU: FOC computation:            ~5-10 µs (estimated)
MCU → FPGA register write:       ~0.1 µs
FPGA PWM update:                 ~0.02 µs
────────────────────────────────────────────
Total estimated:                 ~6-11 µs
Margin:                          ~9-14 µs
```

This timing budget is achievable because signal acquisition (steps 1-3)
and signal generation (step 6) are handled entirely by the FPGA in
parallel with MCU computation. The MCU only performs math.

**Why this matters for precision:**

Two encoders per axis (one on the motor shaft, one on the output after
the reducer) are read simultaneously by the FPGA. At 50 kHz, the robot
corrects its position every 20 µs. This high update rate, combined with
dual-encoder feedback, compensates for reducer backlash and mechanical
imperfections in software — reducing the need for expensive, high-precision
mechanical components.

Scaling to 100 kHz (10 µs) is architecturally possible by using a faster
MCU or offloading parts of the FOC computation to the FPGA, with no
changes to the system architecture.

---

## 6. Mechanical Architecture

### 6.1 Kinematic Configuration

The robot is a serial-link articulated manipulator. The prototype
implements 3 axes (for concept validation), with the architecture designed
to scale to 6 axes.

The mechanical structure consists of modular, standardized elements
connected via a 20mm shaft interface. Each joint is driven by a BLDC motor
through a balanced cycloidal reducer and a belt final stage.

```
[Base] → [Slew Drive: Axis 1 (rotation)]
              → [Cabin]
                   → [Shoulder Module: Axis 2 (pitch)]
                        → [Shoulder Module: Axis 3 (pitch)]
                             → [End Effector / Tool]
```

### 6.2 Slew Drive (Rotary Support)

The slew drive provides Axis 1 rotation. It consists of three 3D-printed
parts:

- **Stator:** A circular base with bolt holes for mounting to the base.
  It has an outer wall and an inner wall forming a rectangular channel
  (raceway) in which bearings ride.
- **Rotor:** A ring that fits inside the stator bore with finger
  protrusions around its circumference. Bearings are pressed onto the
  fingers and ride in the stator channel.
- **Cover:** A ring that bolts onto the stator, closing the channel and
  constraining the bearings axially.

The assembly creates a rigid constraint that allows free rotation while
preventing tilting (nodding) of the robot. The stator raceway is expected
to wear over time with 3D-printed materials and will be reinforced in
future iterations.

### 6.3 Cabin

The cabin connects the slew drive (Axis 1) to the first shoulder joint
(Axis 2). Its design is inspired by industrial heavy equipment
(excavators), where the rotation axis is offset from the arm attachment
point:

- The arm attaches to one side via two bearing ears forming a U-shaped
  yoke.
- The opposite side houses the motor and reducer for Axis 2, acting as a
  counterweight.
- This layout eliminates the tuning-fork resonance effect, increases
  structural rigidity, and partially balances the arm when fully extended.

### 6.4 Shoulder Module

The shoulder module is a standardized structural link. It consists of:

- **Base end:** Two ears that clamp onto a 20mm shaft using hex nuts and
  bolts (6 bolt points per ear), providing a rigid connection.
- **Truss section:** A lightweight lattice/truss structure for
  stiffness-to-weight optimization. Walls are 5mm+ PETG with 100% infill.
  Four 8mm steel rods run inside the truss as internal reinforcement,
  creating a composite structure with rigidity comparable to aluminum
  tube of similar cross-section.
- **Head end:** A U-shaped yoke with bearing bores for the next joint's
  shaft, plus mounting points for the Backpack module.

Multiple shoulder modules can be chained using the same 20mm shaft
interface to extend the arm. The prototype uses a long module and a short
module.

### 6.5 Backpack (Motor + Reducer Mount)

The Backpack is a box-shaped module that mounts underneath the shoulder
module's head, attaching to the same interface used for the yoke. It
serves multiple purposes:

- Houses the motor and reducer for the next joint.
- Stiffens the yoke ears, eliminating tuning-fork resonance.
- Shifts the center of mass closer to the previous joint axis, reducing
  dynamic loads.
- Aligns the reducer output shaft and belt drive with the joint axis.

### 6.6 Balanced Cycloidal Reducer

The reducer is a custom-designed, 3D-printable balanced cycloidal drive.

**Specifications:**

| Parameter | Value |
|---|---|
| Reduction per stage | 10:1 |
| Stages in prototype | 2 (= 100:1) |
| Maximum stages (by volume) | 3 (= 1000:1) |
| Belt final stage | 1:3 |
| Total reduction (prototype)  | 300:1 |
| Form factor | Fits in the palm of a hand |

The high reduction ratio is necessary because the design uses high-RPM,
low-torque BLDC motors. The architecture allows any motor to be used — if
high-torque motors are chosen, the reducer can be simplified or removed.

**Key discovery during development:**

For a rigidly connected, balanced (counter-rotating) dual-disc cycloidal
drive, the standard clearance formula does not apply. The correct formula
for the hole diameter in the cycloidal discs is:

```
Hole_Diameter = Pin_Diameter + (4 × Eccentricity)
```

This is **double** the clearance required for single-disc or independently
suspended designs. This finding was validated through physical testing.

> Detailed development history and the reasoning behind this formula can
> be found in the [Development Log](DEVLOG.md).

### 6.7 Base

The prototype base is a heavy concrete block. An earlier plan to 3D-print
a plastic base was abandoned because it would have required over 2 kg of
plastic while still being too light to provide adequate stability. The
concrete block is cheap, heavy, and meets all requirements.

---

## 7. The Technologist Module: Design Philosophy

The Technologist Module is the most architecturally significant part of
this project. It is what differentiates this robot from others at a
fundamental level.

**The problem it solves:**

Most robotic arms tightly couple the control software with the robot
hardware. Changing the robot's task means rewriting code, reconfiguring
the controller, and often physically modifying the system. This makes
robots expensive to deploy and inflexible in practice.

**The solution:**

The Technologist Module separates *what the robot does* from *how the
robot moves*. The robot's internal control system (FOC, kinematics,
trajectory planning) is a sealed black box. The Technologist Module
communicates with this box through a simple, high-level API.

**What this enables:**

- **Tool independence:** The module controls the tool directly. The robot
  only positions it. Swapping tools means swapping modules.
- **Protocol independence:** The module can communicate with the outside
  world via any interface — Ethernet, EtherCAT, USB, CAN, Wi-Fi, or
  simply execute a pre-programmed sequence from flash memory. The robot
  does not care.
- **Rapid deployment:** A new application requires designing only a small
  PCB with a microcontroller and a PCIe connector. The robot, its
  firmware, and its calibration remain untouched.
- **Clustering:** Multiple robots can be synchronized via the hardware
  clock signal exposed on the Technologist Module connector. This enables
  multi-robot cooperative tasks (e.g., holding a workpiece with one robot
  while another machines it).

**Physical form:**

A small PCB with a microcontroller, a PCIe edge connector, and
(optionally) an external communication interface. It plugs into the
dedicated slot on the Motherboard and is powered by it (5V or 3.3V).

---

## 8. Design Principles

1. **The robot is a black box.** It moves a point in space from A to B.
   Everything inside stays inside. Everything outside stays outside.

2. **Modularity over monolith.** Every subsystem — mechanical and
   electronic — must be independently testable, replaceable, and
   repairable. A Blade swap should take seconds. A shoulder module swap
   should take minutes.

3. **Precision through speed, not mechanics.** Industrial robots achieve
   precision through expensive, ultra-tight-tolerance mechanical
   components. This robot achieves precision through a fast control loop
   (50 kHz) with dual-encoder feedback, correcting mechanical
   imperfections 50,000 times per second.

4. **Infinite scalability (as a goal).** The architecture should allow
   adding more axes, more sensors, and more robots without fundamental
   redesign. The FPGA's parallel nature makes this feasible for I/O.
   The standardized mechanical interfaces make this feasible for
   structure.

5. **Power agnosticism.** The robot should accept any DC power source
   from 8V to 60V. If it can be deployed anywhere, it should be powered
   from anywhere.

6. **Accessibility.** The robot must be buildable by anyone with a 3D
   printer and common tools. The BOM cost should be comparable to a
   power tool, not an automobile.

7. **Reusability.** Like good code, no part of the robot should be
   single-purpose. The shoulder module is the same for every joint. The
   Blade is the same for every axis. The reducer is the same at every
   stage.

8. **Motor agnosticism.** The control system must work with any BLDC
   motor. The system should be able to characterize an unknown motor
   and configure itself accordingly.

9. **The tool defines the task, not the robot.** Swapping the
   Technologist Module and the end-effector changes the robot's purpose.
   Today it mills. Tomorrow it welds. The robot itself does not change.

10. **Mechanics is necessary but not primary.** We cannot build a robot
    from sticks, but we also must not rely solely on mechanical precision.
    A $50,000 harmonic drive on a poorly controlled system is still a
    poorly controlled system.

---

## 9. Target Specifications

| Parameter | Prototype (3-axis) | Target (6-axis) |
|---|---|---|
| Degrees of freedom | 3 | 6 |
| Control loop frequency | 50 kHz (20 µs) | 50–100 kHz |
| Input voltage | 24V DC | 8–60V DC |
| Current per axis (nominal) | 4 A | configurable |
| Current per axis (peak) | 10 A | configurable |
| Power per axis (nominal) | ~100 W | ~150–300 W |
| Encoder resolution | TBD | TBD |
| Encoders per axis | 2 (motor + output) | 2 (motor + output) |
| Reducer ratio | 300:1 (100:1 + 1:3) | up to 1000:1 + belt  |
| Motor type | BLDC (any) | BLDC (any) |
| Positioning accuracy (target) | < 0.1 mm (with cal.)  | < 0.05 mm (with cal.)|
| Payload | TBD | TBD |
| Reach | TBD | TBD |
| Robot mass (estimated) | TBD | TBD |
| Electronics BOM (3-axis) | ~$80–120 (estimated)  | TBD |
| Frame material (prototype) | PETG (3D-printed) | Aluminum (milled) |
| Blade swap time | Seconds | Seconds |
| Technologist Module swap time | Seconds | Seconds |

---

## 10. Current Status and Roadmap

> For detailed week-by-week progress, see the [Development Log](DEVLOG.md).

### Completed

- [x] Core mechanical design (3-axis CAD)
- [x] Balanced cycloidal reducer (designed, printed, assembled, tested)
- [x] Shoulder modules (printed and assembled)
- [x] Slew drive (printed and assembled)
- [x] Power Blade schematic design
- [x] Power Blade PCB layout and routing
- [x] Component simulations (DC/DC, current amplifier, half-bridge)
- [x] FPGA core (PWM generator, dead-time, encoder decoder, CSR, SPI master)
- [x] ADC-to-SPI pipeline on STM32G431 (~400 ns latency)
- [x] Gerber/BOM/CPL files generated
- [x] PCBs ordered and received
- [x] Power Blade power-on test (all voltages verified)
- [x] FOC algorithm implementation on STM32H7 (Clarke, Park, PI, SVPWM)
- [x] Full control chain validated: ADC → FPGA → MCU → FPGA → motor (20 kHz)

### In Progress

- [ ] Remaining mechanical assembly (shoulder fitting, belt tensioning)
- [ ] Motor spinning on Power Blade (transitioning from dev boards)
- [ ] Motherboard schematic design

### Future

- [ ] Motherboard PCB design
- [ ] Technologist Module prototype
- [ ] Input Power Board
- [ ] Position/velocity servo loop
- [ ] Inverse kinematics
- [ ] Multi-robot clustering
- [ ] Calibration system (reference flat surface)
- [ ] Aluminum version (self-manufactured)

---

*Project started: May 27, 2025*
*This document reflects the architecture as of the prototype development phase.*
*For component details, see [components.md](hardware/docs/components.md).*
*For development history, see [DEVLOG.md](DEVLOG.md).*

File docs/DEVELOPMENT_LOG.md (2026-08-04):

# 2025-08-13: The Project is Public!

## Milestone
Today, I've made the repository public and started this development log. This marks the official start of the public phase of the project.

## Current Status
The majority of the conceptual CAD work for the core 3-axis mechanics is complete (around the 90% mark). I've been so focused on design iterations and preparing for the first printing tests that I haven't committed the CAD files to the repository yet.

## Next Steps
My immediate goal is to clean up the models and push the complete set of F3D/STEP files to the /cad directory by this Saturday (August 16th).

## Comment
If someone rly see this **hey,have a nice day! :>** i hope what i make that to this saturday cuz with this i need to start making PCB its little scary but we need this to 50 kHz. <Cya> 

## 2025-08-24: Stage II Begins - Electronics & First Working Prototype!

### Milestone
This weekend marks the official start of the electronics development phase. The core mechanical and electronic architectures are now finalized. Most importantly, the first PLA prototype of the 10:1 reducer module was printed, assembled, and **it works flawlessly!**

### Current Status
Following the successful test of the 10:1 reducer, I will be uploading its final STL files to the /manufacturingdirectory. The PDF overview of the electronics architecture is now also available in/hardware/docs.

The initial assembly of the reducer revealed a critical kinematic conflict: the drive did not work. After analysis, I identified a mistake in the clearance calculation for the output flange fingers. The holes in the cycloidal discs were recalculated and enlarged, which completely solved the issue.

### Next Steps
The primary focus now shifts to designing the **Power Blade** electronics. In parallel, I will continue printing and testing the complete mechanical assembly. I'm considering creating a **Telegram channel** to post real-time development updates, including videos and failures. Let me know if you'd be interested!

### Comment & Key Discovery
I have to admit, when the first reducer assembly seized up, I was worried about the entire design. But after thinking through the kinematics, I realized a fundamental principle for balanced cycloidal drives with a rigid output cage.

The standard formula for hole clearance, Hole_Diameter = Pin_Diameter + (2 * Eccentricity), is only valid for a single-disc or independently suspended dual-disc setup.

For a **rigidly connected, balanced (counter-rotating) dual-disc setup**, the required clearance is doubled. The correct formula is:

**Hole_Diameter = Pin_Diameter + (4 * Eccentricity)**

This was a scary realization, as it required making the holes in my very compact reducer significantly larger. However, the design had enough material to accommodate this. After reprinting the discs with the corrected hole diameter, the reducer works perfectly. This is a crucial finding for anyone building this type of drive.

This week, I will try to develop the full Power Blade schematic. And again i write this at midnight... <Cya guys, sleep well>

## 2025-09-02: Little sick but with power blade architecture!

### Milestone
Power blade architecture is DONE! The short shoulder module is printed.

### Current Status
The architecture was a little easy for me because I had been thinking about it for two weeks, so I just sat down and made it. But with printing, I am continuing my war with the 3D printer. It just stopped in the middle of the night while I slept and ruined about 90% of the print. I need to start again and buy more plastic, but the printer is far from me, so I will restart printing next weekend ":/"

### Next Steps
The next step is to totally finish the blade's schematic and start to test it in SPICE programs. In parallel, I need to pick components for the blade. And of course, printing, printing, printing....

### Comment & Key Discovery
All week I was sick, and after work, I just lay in bed and thought about how much I needed to do but couldn't. BUT on the weekend, I was fine and finished the architecture. That was a victory! -^-

## 2025-09-07: POWER BLADE SCHEME IS 90% DONE!!

### Milestone
Power blade scheme is 90% done. Printing new shoulder module.

### Current Status
Updated settings for 3D printer and start printing part of shoulder module again. Ears printed and i think it okay. Today i buyed shafts and other steel staff they gonna come like... 2-3 weeks... I added datasheets and file "components" for (You won't believe it :> ) components for boards and add all components for axis channel. My win today is scheme power blade done on 90% its just need to make footprints and past. Ye i needed to test power blade today in spice program but without footprints its unreal and i dont make it not proud for that..

### Next Steps
The next step is stay same test and finishing scheme and after i can make pcb.

### Comment & Key Discovery
**DAY NOT OVER WHILE I DONT LAY!** 
Weekend again was hard cuz i have no time for help familly and no time for this robotic arm, but i sit here and now is totaly early morning i writing this and go to sleep. Printer is printing night going to over. on this week i will be study and work and free time on week is die. Have a good night guys <cya>

## 2025-09-14: Real-World Assembly & Design Evolution

### Milestone
The first full two-stage reducer prototype was assembled and tested. While encountering critical issues, the tests successfully validated the core kinematic design and led to a significantly improved and more robust architecture.

### Current Status & Key Discoveries
This weekend was dedicated to the first physical assembly of the two-stage balanced cycloidal reducer. The test was a partial success:

    The Good: The core mechanism works. When assembled, all parts fit, and the kinematics are correct — the drive rotates and provides reduction. The new, longer stator pins, when press-fitted (with a hammer), provide excellent structural rigidity without interfering with the cycloidal discs' motion.

    The Bad (Problems Found):

        Structural Failure: The bottom wall of the main reducer shaft proved to be too thin. It cracked and crumbled under the stress of assembly (e.g., inserting an M8 nut).

        Stator Pin Instability: The stator pins were not sufficiently constrained and could be dislodged, leading to mechanism failure.

    The Ugly (Resource Loss): Lost two major prints (~800g of PETG and ~40 hours of print time) this past week due to a corrupted SD card file and suboptimal print settings that caused delamination. This is a painful but valuable lesson in process reliability.

### Design Evolution (The Solutions)
Based on the test results, I've developed a new, more robust design:

    Motor-to-Reducer Coupling: The initial concept for the input shaft was flawed. The final design will be: a pneumatic collet fitting (with metric M6 thread) screwed into a heat-set brass insert in the 3D-printed reducer shaft. The entire assembly will be locked by a transverse pin ("the nail") secured with a retaining ring. This provides a robust, balanced, and modular interface.

    Stator Assembly: The stator pin instability will be solved by:

        Closing the open holes in the stator plates.

        Adding an intermediate stator plate between the two stages for added support.

        Increasing the contact surface area between the stators and the pins.

The CAD models will be updated with these improvements next week. The only potential delay is sourcing the non-standard M6 heat-set inserts.

### Next Steps & Plan Adjustment
The initial plan to start the PCB layout this week is postponed. The unexpected but critical mechanical redesign takes priority.

    This Week (Evenings): Continue with the Power Blade schematic design. The goal is to have it 100% complete by the next weekend.

    Next Weekend: Finalize the mechanical redesign in CAD and begin printing the new, improved parts.

    Documentation: I will update the repo with the final printer settings, add component libraries, etc.

### Comment
This was the first major "slip" in the schedule due to the demanding university timetable and unforeseen design flaws. I had planned to be working on the schematic this weekend but spent almost all of it on mechanical assembly and problem-solving. This is frustrating but also incredibly productive. The design is now an order of magnitude better.

In same situations i remember this quote:

    You know, the world isn't run by the laws written on paper. It's run by people. Some according to laws, others not. It depends on each individual how his world will be, what he will make of it... I dreamed of fortunes, cars, freedom, women, respect... I got it all more or less, but with it came prison, constant fear, and the blood of my comrades.

    — Mafia: The City of Lost Heaven

But unlike that story, **we don't give up so easily.** There is more to come and rest will be after revolution in robots :)

Thanks for following along. <Cya guys!>

## 2025-09-15: little steps 

### Milestone
I finished schematics for components everything except `ADC` and add `PRINTER.md` to docs 

### Comment

**I think for little commits on week i will be use milestones and comments, cuz i cant doing many work for my robot and u can see other information like next steps u can see upper.**

For today i maked 2 scheme of components DC/DC and LDO 5V and i bought components for connect reducer shaft and motor shaft. after they come i assembly reducers and test it and i think now that will be immortal connection ~~(sounds like joke)~~ but anyway we can see it later. For other i add my config for 3d printer to `docs/guides/PRINTER.md` u can check what settings i using for printing mb its can help u :)

## 2025-09-16: schematics for components are completed !!!

### Milestone
I completed scheme for STM32G4 and add all schematics to repository !!!!!

### Comment
So so so that was too long for one component but all functions for every pin from datasheet in schem and that now have footprint. 
I change MC cuz i little mistake with price for `STM32G474CEU6` u can read about that to `hardware/docs/components.md`. time to sleep.. <Cya>

# 2025-09-23: Principle scheme is complete!

## Milestone
Completed the schematic; simulations and printing are underway

## Current Status
I completed the schematic, started printing the second part of the shoulder module, and successfully assembled the shoulder module on the shaft. I also started the simulation using the INA240 in LTspice

## Next Steps
Finish simulations and start PCB design and create a Telegram channel

## Comment
This weekend was tough: I started around 9:00 PM and worked until about 4:30 AM on Saturday and 5:00 AM on Sunday. On Monday I worked and fixed the schematic — the pin headers for the joke turned out to be harder than 60% of the circuit design. I spent 4 hours figuring out how to use PCI — it's just a connector I can use for the board. Before that I considered a mezzanine connector but couldn't find one compatible with my board that didn't cost almost as much as the whole board with all components. Now we're using PCI at a reasonable price. During the week I will create a Telegram channel to document activity like videos and fails, since using Git for that is inconvenient; I'll be there all week.

# 2025-09-23: Simulation INA240 are complete!!!!

### Milestone
* Add all spice schematics for axis channel blade
* Create directory `simulatons` 
* Made 4 simulations for `INA240` amplifier.
* Made telegram channel 

### Comment
All week i working and afer work i just lay and its all what i did and that will be true if i was a just good worker who woudnt sleep tomorrow, for that after work maked simulations and learn LTspice...khm.. i working in this program before but with simple simulations and now i tryed be serios so today we have complete simulation for first component! <Good night~>

# 2025-09-28: ALL SIMULATIONS COMPLETE. STARTING PCB!!!!

## Milestone
Completed all simulations and the final schematic for the Axis Channel. Remodeled the head of the shoulder module and the shaft for the 10:1 reducer.

## Current Status
- **Simulations:** Successfully completed and verified the DC/DC, Current Amplifier, and Half-Bridge circuits.
- **Documentation:** Created a guide on how to import SPICE models.
- **CAD:** Remodeled the shoulder modules and the reducer shaft. Started printing the main shoulder part.

## Next Steps
- **Start the PCB layout** for the Axis Channel blade.
- **Finish** the CAD models for the reducer and shoulder assembly.

## Comment

I thought the simulations would be the easy part - just load models and run. The DC/DC simulation, on the other hand, was done in 30 minutes. The half-bridge, however, took an entire day just to get it to work at all.

In the end, I got the basic simulation running and saw the square waves, which is a success. Honestly, I hoped to simulate a real "hell" scenario for it with all the parasitics and protections, but that's a project in itself, and I just don't have that much time to spend only on simulations.

So I made a pragmatic engineering decision: I based the final schematic on proven reference designs from datasheets and application notes, using LTspice just for a basic "does it switch?" sanity check, without the deep, "hard tests". It's a calculated risk, but a necessary one to move forward.

Now, I continue my war with the reducer models. It needs so many iterations of printing parts, which is not easy when I can only print 2 days a week. I spent most of this weekend just modeling because I messed up the sizes for the main shaft bearing... I don't know how it happened, but it is what it is.

So, time is again not on my side. Looks like another night of 4 hours of sleep... Thanks for your attention, have good dreams :)

# 2025-10-06: SCHEMATICS ARE DONE. PCB HELL BEGINS.

## Milestone
* Started printing the lower part of the long shoulder module.
* Configuration of Altium for starting the PCB is over.
* Created all remaining components for the Axis Channel blade with their footprints.
* Imported all components into the PCB project.

## Current Status
- **Schematics:** Replaced all default Altium components with my own custom ones.
- **Libraries:** Built a complete library with every single component for the Axis Channel blade.
- **PCB:** The PCB file is created. The board outline is set to 100x100mm. The layer stack is defined. All components have been imported.

## Next Steps
- **PCB:** FINALLY START IT!!!!!
- **CAD:** Continue printing and assembling parts.
- **LTspice:** Run one or two more simulations for the LDOs.

## Comment

It's 3:40 AM on a Monday morning.... **[dying sounds]**

That was insane, really. So many hours creating footprints, hunting for datasheets, and fighting with Altium settings. But it's finally over. We are starting a new part of this strange story!

**AND for now!!!** <Have a good night, guys :)>

## 2025-10-13: PCB Hell might not BEGIN, but it could start this week...

### Milestone
* Finished printing the long lower part of the shoulder module.
* <I use Arch btw>...
* Completed simulations for the 12V, 8V, and 5V DC/DC converters.
* Corrected the DC/DC schematics in Altium and validated them in LTspice.

### Current Status
- **Printing:** The lower part of the shoulder module is done. The new support settings are working well.
- **LTspice:** Finished the DC/DC simulations and found a major problem in my original schematic. I'm not sure how it even worked before, but it's correct now. In short, I had issues with the feedback and COMP circuitry. It's fixed now.
- **Altium:** Corrected the Axis Channels chematic. I will start the PCB layout this week.
- **Arch:** Installed Arch Linux on my new laptop. I'll be using it for all STM programming and other development.

### Next Steps
- **PCB:** FINALLY START THE LAYOUT! ~~(This time for sure...)~~
- **CAD:** Print the upper part of the shoulder module.
- **Arch:** Finish configuring the development environment.

### Comment
This weekend was just tr... khm...

I forgot my laptop charger in another city, so the entire weekend was lost, and I literally did nothing. However, on Saturday, I received my new laptop ~~(a ThinkPad, running Arch btw)~~ which was the only good news.

I spent all of Saturday evening and all of Sunday installing Arch(~~on a ThinkPad, btw~~) and just finished it today.

Now I have the proper tool for thepost-PCBsteps. Today, I managed to fix the schematics and finalize the DC/DC simulations.

That was just some bad luck, and I hope it's the last bad weekend for a while ~~(nope)~~.

Thanks for your attention, <have a good night!> :)

# 2025-10-20: WE ARE BACK! 55% OF THE DRIVER IS DONE.

## Milestone
* Started printing the long upper part of the shoulder module.
* Completed the placement of all main power components (half-bridges, amplifiers, gate drivers).

## Current Status
- **Printing:** I've started printing the upper part of the shoulder module after making fixes to the CAD model.
- **Altium:** The Axis Channel schematic is fully corrected. This week, I'm diving deep into the PCB layout.

## Next Steps
- **PCB:** Finish component placement and begin the routing phase.
- **CAD:** Test assemble the long shoulder module and buy the 10mm shafts.

## Comment

This was just a very good weekend, and I can't comment on that any other way.

Everything I wanted to do, I did!

I spent all night on the placement of the MOSFETs, and along with them, I placed the amplifiers and gate drivers. And that's just... finally, it's done!!

`Just start the task.`
        `Just finish the task.`
                `That's how I will build this robot!`

<Have a good night, guys :)>

# 2025-10-21: Little Refactor

## Milestone
* Refactored the entire placement of the main power stage components. The primary goal was to drastically shorten the path from the gate drivers to the MOSFET gates.

## Comment
Before this refactoring, the trace length to the upper MOSFET's gate was around `~10mm`. After a complete re-layout of the power core, the new path is now only **`1.5mm - 1.8mm`**. This is a massive improvement that will significantly reduce gate loop inductance, leading to faster, cleaner switching and lower thermal losses.

# 2025-10-27: Placing is Over

## Milestone
* Finished placing the RS-485 receivers, the MCU-ADC, and the 5V DC/DC converter.
* Started printing the long upper part of the shoulder module... again...
* Tested new hole sizes for the pins in the 10:1 reducer.
* Dialed in new settings for Orca Slicer.

## Current Status
- **PCB:** I've finished placing 90% of the components. The last 10% are the two remaining DC/DC converters.
- **Printing:** This weekend's main theme. I broke the upper part of the shoulder module while trying to fit a bearing. After that, I changed my settings and printed a new stator, shaft, and outer flange. Then I started printing the upper part of the long shoulder module again. And, to top it off, I broke the lower part of the short module during assembly. It was a bad print from the start and was just defective all this time.

## Next Steps
- **PCB:** Finish component placement and begin the routing phase. ~~(Still same)~~
- **CAD:** Test assemble the long shoulder module and buy the 10mm shafts.

## Comment

Just an insane weekend. I finally finished the majority of the placement, and I think the routing will be easy because all the components are placed very close together, allowing me to use copper pours for many connections.

I broke TWO parts this weekend... AAAA... *khm*. But now I know that one of them was trash from the beginning, and the second one *can* fit the bearing, but only if you don't use a hammer...

A very good weekend. I hope the same for you :)

<Have a good night, sleep well guys>

# 2025-11-03: Little Necessary Work

## Milestone
*   Finished component placement for the Axis Channel blade.
*   Finished printing the long upper part of the shoulder module.

## Comment
Just some necessary work is done. Tomorrow, the plan is to finish the reducer assembly, start the PCB routing, and begin printing the lower part of the short shoulder module.

And now... <have a good night~>

# 2025-11-09: FINALLY, LAYOUT!

## Milestone
*   Replaced the MCU and its supporting components on the layout.
*   Completed the initial routing for the entire Top Layer of the Axis Channel blade (~50% of total routing).

## Current Status
- **PCB:** Literally what I said above, haha.
- **Printing:** The new head for the long shoulder module broke because the layers didn't merge properly. When I tried to press-fit a bearing (gently, really!), it just went *CRRRRR* and... *khm*. Anyway, I'll be reprinting this part (this will be the third try).

## Next Steps
- **PCB:** Finish routing!
- **CAD:** Print the head of the long shoulder module *again*, and finally `buy the 10mm shafts`.

## Comment

Phew... it's 4 AM again, and I'm sitting here, trying to make little steps to create this thing. I was a little sad when the shoulder module part just broke again, but then I tried pressing a bearing into the second hole, and it didn't break! It even held up while I was pressing it in, which gives me hope :).

I've also made a decision: first, I'll finish the routing, and *second*, I'll place the PCIe connector on the schematic. I need to understand where the routes can connect to the PCIe connector most efficiently to create the shortest paths, and only then will I finalize the connections on the main schematic.

After the part broke, I just took a hammer and smashed it to see how good the infill was. And honestly, it wasn't bad. Of course, it could be better, but it's a really solid plastic part. When I hit it, it just deformed, and only after about 10 hits did it shatter into small pieces. Yeah, some walls looked like they weren't solid, but maybe that's just the limit of 3D printing, because when I hit it, it reacted like a solid part.

So, yeah... I think it's time to sleep. <Have cool dreams~>

# 2025-11-10: Updated settings for Orca

## Current Status
- **Orca slicer** updated orca slicer settings

## Comment
U know what ?? `updated orca slicer settings!!` ~~(insane right?)~~

# 2025-11-16: Little Steps in Layout

## Milestone
*   Successfully assembled the head-shoulder module.
*   Learned all about vias. 
*   Made the layout for the GND and PWR planes.
*   Finally bought the 10mm shafts.

## Current Status
- **PCB:** I spent the entire day trying to figure out how to properly place vias for the GND and PWR planes, but now I finally know how to do it. And now, I need to go to sleep :(
- **Printing:** Finally pressed the bearings in without breaking the part! Now starting to print the base.

## Next Steps
- **PCB:** Finish routing the bottom side!
- **CAD:** Print the base.

## Comment
This weekend felt very short. I had to visit a lesson at the university this week, which is in another city, and by the time I got back, a day was gone.

So I only had one real day, and I spent all of it just understanding how to place vias correctly. For now, I need to go to sleep, but at least I know how to do it. I think the actual work of placing them will be pretty simple and fast now.

<have a good night guys ~>

# 2025-11-18: THE BEAST HAS A NERVOUS SYSTEM

## Milestone
* All signal paths are now routed.
* The "quiet" side of the board is essentially complete.

## Comment
I like how it's going. I think we can do it.

<Have a good night, guys. We're almost there.>

# 2025-11-24: LAYOUT - OVER.

## Milestone
*   **PCB:** Finished the PCB Layout / Routing.
*   **Mechanics:** Tested the new connection mechanism between reducer stages (Success).
*   **Printing:** Started printing the stator for the rotary support.

## Current Status
-   **PCB:** Yeah, we did it. The next step is a final error check (DRC), ordering the boards, and then... the scary part: Programming.
-   **Printing:** The base wasn't printed because the extruder got stuck/clogged. But I did some thinking... why spend 5kg of plastic on a base that will still be lightweight? I decided to use a **cheap, heavy concrete block** instead.
    *   Started printing the rotary support (had to cut angles slightly to fit the print bed).
    *   Spent 4 hours fixing the jammed extruder. Learned a lesson: after cleaning plastic and reassembling, you need to give the printer time to "chill," or the thermal sensor won't work right.
-   **CAD:** Designed a new mechanism to connect the two reducer stages. I made vertical slots for steel pins in the shaft, slots in the outer flange, and an 8mm plastic pin in the center for alignment. It's perfectly centered now.

## Next Steps
-   **PCB:** Order the boards!
-   **CAD:** Print the rotor for the rotary support.

## Comment
Okay, I can only sleep 4 hours again, but I finished the layout and wrote this log.

The next stage — Programming — is coming, and it's a little scary because the other stuff isn't fully finished. Drivers need to be ordered, mechanics aren't fully printed... but we need to go down this road. We can't stay still — that is the main rule.

The order itself is a challenge. Waiting 1 month... for what? To potentially see fire from my board and then wait 1 month again? It's a risk, but I knew these nuances from the start. I understand them.

If it really works... I can't imagine how happy I will be.
And next month — exams. That's also a challenge.
So, conditions are not friendly. But when were they ever? :)

We broke through it.
<Have a good night, sleep well guys>

# 2025-12-19: ALIVE!.. Maybe Alive...

## Milestone
*   Gerber, BOM, and CPL files for the Axis Channel blade are generated and ready for production.
*   The 3D printer's hotend has been replaced; printing has resumed (after a month of waiting).
*   Fixed the main problem with the reducer.
*   `components.md` has been refactored into a more structured format.

## Current Status
-   **PCB:** Waiting for the "go" signal from my contact to place the board order. The logistics are complicated, so this is currently on hold.
-   **Firmware:** The lab bench is set up. I have a dev board for motor control, the STM32H7A3 dev board, a Tang Nano FPGA board, three BLDC motors, optical and magnetic encoders, a lab PSU, and a ton of wires. The goal for this month is to get the core firmware up and running.
-   **Printing:** The new hotend is installed. Tried to print the massive slew drive. The part is warping and lifting, but I will fix it. I think it's bad settings or G-code, but I'll probably need to build an enclosure for the printer anyway...
-   **Documentation:** I completely rebuilt `components.md`. The old "just throw it in" style was great for brainstorming but terrible for actual work and comparison. The new version is structured and much more usable.

## Next Steps
-   **Firmware:** Start writing and debugging the core firmware on the dev boards.
-   **PCB:** Push for the board order.
-   **CAD:** Successfully print the slew drive and the reducer parts.

## Comment
It feels like a whole month just vanished. The last commit was on November 24th...

Between work getting intense (late nights, releases) and university exams hitting hard, the robot had to take a backseat. I spent days that should have been for studying on generating production files, and now... waiting for logistics.

It's frustrating. While the boards are in limbo, I need to finish my exams and, on my free days, start the firmware. I have everything I need to start writing and testing the code. By the time the real hardware arrives, the firmware should be 80% ready.

Just sorry for this month... ~~it will happen again.~~

<Have a good night, guys. The fight continues.>

# 2025-12-24: General Kenobi!

## Milestone
*   Updated components.md.
*   Successfully printed the slew drive.

## Comment
You know how I'll name the next dev log... *khm*.

This month was dominated by exams, and I just couldn't work on the robot full-time. But now, with the last exam of the year on Dec 26th and the next one not until Jan 11th, I'll have plenty of time to develop the firmware.

The guy who's ordering my boards says he's ready to try and place the order in the coming days.

Printing is going well, too! I made a cardboard enclosure for my printer, and the slew drive was successfully printed with new, faster settings.

It was a hard month, but now I believe it's over, or at least it's giving me a little break. Anyway, we are reaching the middle point of the project!

Thanks for your attention :)

<Good night, guys :))>

# 2026-01-03: Hello there!

## Milestone
*   **FPGA Core:** Successfully completed ~80% of the FPGA code.
*   **CAD:** Started printing the final version of the reducer.~~(and fixed the printer)~~

## Current Status
-   **Firmware:** Written the modular architecture in SystemVerilog.
    - `system_storage`: The CSR brain of the axis.
    - `pwm_generator`: Center-aligned PWM for FOC.
    - `deadtime`: Hardware protection for MOSFETs.
    - `quadrature_decoder`: Glitch-filtered encoder reading.
    
    *Key Discovery:* Spent some time fighting with the encoder signal. Turns out the Omron encoder with Open Collector output needs strong external pull-up resistors to 3.3V. Once added, the FPGA saw the signal instantly.

-   **CAD:** 
    -   **Upgrade:** Installed a new PEI build plate.
    -   **Repair:** Fixed critical mechanical play in the printer. It turns out the toolhead was misaligned due to an assembly error. I tightened all the V-wheels, and now everything is working fine.

## Next Steps
-   **Firmware:** Connect the PWM output to the real gate driver and finalize the FPGA core.
-   **PCB:** Push for the board order.
-   **CAD:** Finish printing reducer parts and start printing the rotor for the slew drive.

## Comment
It's 2:00 AM.

Sleep is.. what is this.. khm..

FPGA is very interesting, very strong, very fast AND!! very scary!!

Honestly, I just can't understand it sometimes... **Assembler feels easier!!!**

But after two days of trying to decipher these hieroglyphs, I finally started to understand, and to be honest — it's simple. On an STM32, you have a thousand functions with strange names and you need to know them all. But on an FPGA, you just have logic gates that haven't changed in the last 100 years. It feels like playing chess for the first time.

As for CAD, I'm so glad for the new PEI plate. The adhesion is insane — I actually need to heat the plate just to remove PETG parts. 

I also fixed the backlash today. Spent 3 hours on it because I had to disassemble the entire printer, reassemble it, realize I missed something, disassemble it again... aaaaand finally assembled it right.

<Have aaaa very good night guys :) Happy holidays!>

# 2026-01-06: FPGA CORE COMPLETE!

## Milestone
*   **FPGA Core:** Successfully completed the FPGA core architecture.
*   **CAD:** Printed and assembled the final version of the reducer!!!
*   **PCB:** Boards are ordered.

## Current Status
-   **Firmware:** All FPGA modules are written and verified. The FPGA is ready to connect to the MCU and drivers to spin the motor! But... this also means I now need to write the code for the MCU.
-   **CAD:** I assembled the reducer and it works!! It's a little tight (I will adjust tolerances in the next iteration), but... **GUYS, IT'S A 100:1 RATIO, IT FITS IN THE PALM OF MY HAND, AND IT WORKS!**
-   **PCB:** Boards are finally ordered! In about two weeks, we'll see the Moment of Truth (and hopefully no magic smoke).

## Next Steps
-   **Firmware:** Develop the MCU firmware and connect the PWM output to the real gate driver.
-   **CAD:** Refine reducer tolerances, start printing the rotary support, and update the CAD models.

## Comment

You know what time it is? 2:00 AM! Again!

But I'm just happy because I'm done with the FPGA part and can finally move to the next step of making this robot alive. ^^

<Have a goooood night!>

# 2026-02-08: ADC 400ns without CPU!

## Milestone
*   **FPGA Core:** Updated code to test the new ADC setup and adjusted delays.
*   **CAD:** Successfully printed the rotary support and performed a test assembly.
*   **MCU:** Implemented a bare-metal, zero-CPU-overhead Dual ADC-to-SPI Data Pipeline.

## Current Status
-   **Firmware:** The FPGA core is ready and waiting for the other parts of the system. I've tested the new ADC setup with it, and it works! Latency is projected to be around **400 ns**.
-   **CAD:** I fought with the printer all month for just two parts, but the rotary support is finally finished. I think I've learned all its quirks. (If you really try to build this, I hope you buy a better printer, but my goal is to prove you can make my robot on ANY printer).
-   **PCB:** Still waiting ;-; .

## Next Steps
-   **Firmware:** Make the motor spin using the full chain: ADC -> FPGA -> STM32H7. Maybe even start on FOC.
-   **CAD:** Update the model for the Shoulder_Clevis_Mount and figure out how to print this monster. I think it will eat more than 1kg of PETG.

## Comment

You know what? I can't believe a whole month just passed. I spent almost all of it trying to print, but this printer just didn't want to cooperate. I spent a huge part of my time just trying to understand what I was doing wrong. Two recommendations: 1. Wash your build plate (really, it's insane how well it works). 2. Don't buy an End... *khm*. Change your Z-offset while the printer is printing the first layer, and if it doesn't stick, make the gap smaller.

And the whole month I was fighting with the ADC. I tried to configure it so that when the ADC sends data to SPI, a leg of the MCU would catch it and raise a logic level. But the first week ended with zero results. The second week, I actually made it work, but the gap between the data and the logic signal was **20 µs**. I can't find the words to describe how sad it was to see that. After a whole weekend, I got it down to **6 µs**. A good result in comparison, but VERY, VERY bad for my goal. I need the data after 1-2 µs max; 0.5 µs would be perfect, leaving me 9.5 or 19.5 µs for the other things in the FOC cycle.

I don't know what I was doing in the third week, maybe I just deleted all my SPI and ADC code. But last week, I just sat on it after work and study, like 6 hours a day until 2 AM. And this Friday morning, I finished it. I can see that my ADC is working! It's just unbelievable. And now I've polished the code and even made a Makefile (ha-ha) for easy use later.

Sorry for the long pause, guys!

<HAVEEEEE AAAA GOOOOOOOOOOOOOOOD night :> >

# 2026-02-12: Architecture Document 

### Milestone
*   **docs:** Created `architecture.md` — full system architecture document.
*   **CAD:** Strarted printing shoulder clevis mount (cabin) and it`s eat 970 gr PETG with 80% fill (im happy).

### Comment
2:33 AM. Classic.

many bla bla bla but it is necessary

<Have a good night ~>

# 2026-03-12: The Beginning of the End

## Milestone
*   **FPGA Core:** Finished `top.sv` for FOC, encoder, and ADC. Full system integration complete.
*   **MCU:** Finished FOC implementation and integrated it into the complete system.
*   **CAD:** Printed the last main structural part.
*   **PCB:** Boards are VERY NEAR.

## Current Status
-   **Firmware:** All parts are working together as one system. **My architecture is correct.** On dupont wires, I achieved 20 kHz FOC. The full real-time chain works end-to-end: FPGA reads encoders and ADC currents from G4, packs them into a 256-bit SPI frame, sends to the H7, the H7 runs FOC and sends PWM commands back — all at 20 kHz, on a pile of dupont wires.
-   **CAD:** The shoulder clevis mount is printed. We now have all the parts to start assembling the body of this plastic hero.
-   **PCB:** Boards are coming to my house around March 20th. ~~hope they will work~~

## Next Steps
-   **Firmware:** Freeze while assembling the body.
-   **CAD:** Start assembling all parts of the robot and polish the fit of each piece.

## Comment

We have come to the end of this work, and we will end this at any cost.

I can't get used to the fact that every new step with electronics and code is a month of work. And I really do work on it — sitting for hours, two or more nights a week until 4 or 5 AM, trying, trying, trying again and again. And the funniest part? Not understanding what isn't working. Is it the code? A dupont wire? Did I assemble the circuit wrong? Maybe the encoder is on the wrong side? That uncertainty is the hardest part of all of this.

**But anyway, like everything else, it just needs time. And what can stop me now? Huh?**

**The firmware part is over!**

Let's just remember what I wanted to finish from the start: CAD, PCB, and... firmware. Now we just need to make it all work together. We have all the parts for it.

**Time to finish this.**

**AND NOOOWW..** time to go to sleep.

<Have a good night, good person! :> >

# **2026-04-24: Yep, it's me again. And I'm not dead.**

## Milestone
*   **Docs:** Fixed the `architecture.md` file.
*   **CAD:** Repaired the printer and printed the 60-tooth rollers; designed a motor holder; assembled the shoulder modules; printed and adjusted the actuator module; fixed the reducer models; developed a new 20:1 reducer and ordered materials for it; and finally, assembled and tested the rotary support.
*   **PCB:** Tested all board systems (they work!) and updated the Gerber files.

## Current Status
*   **CAD:** It's been a sea of troubles, but I managed to get everything I listed above done.
*   **PCB:** THE BOARDS WORK! ...well, with one tiny issue. I accidentally shorted a trace under a suppressor in the third half-bridge. A quick fix later, and everything is running smoothly. I've tested the DC/DC converters, spun a motor, and successfully programmed the microcontroller. The Gerbers are updated with the fix, so if you're brave enough, you can order them now.
*   **Docs:** I accidentally deleted the old architecture file. When I finally noticed, I just fixed it. No further comments.

## Next Steps
*   **CAD:** Keep assembling all the parts.
*   **Docs:** Write my thesis.

## Comment
This past month hasn't been the most exciting, I'll admit. There were no major milestone breakthroughs—just a whole lot of grinding. I've been assembling, printing, writing my thesis, and fixing one small issue after another. Sorry for the radio silence on GitHub, but I honestly didn't know what to write. It's not that things are bad, just that it's been a ton of little tasks—all hands-on work, spending money on bearings, shafts, and other hardware.

One interesting discovery: trimmer shafts. They're incredibly cheap, strong enough for the roller bearings, and conveniently 8mm in diameter.

A huge amount of time went into printing. I think the next dev log will be after I'm done with my thesis. If you want to see what I'm up to in the meantime, you can follow my Telegram channel.

Thanks for your attention. **The work doesn't stop.**

<Have a good night>

# 2026-03-12: First axis assembled (almost)

## Milestone
*   **Assembling:** First axis assembly is almost complete.
*   **Base:** Finished the epoxy granite base and uploaded the casting guide.

## Current Status
-   **Assembling:** 2 reducers and the rotary support are fully assembled. Currently trying to screw on the clevis mount.
-   **Base:** hmm... what did I do... forgot..

## Next Steps
-   **Assembling:** Assemble the second axis.
-   **CAD:** Continue assembling all the parts of the robot and polish the fit of each piece.

## Comment

I made the base out of epoxy granite, and it felt like doing stonemason work all day. My room looks like a dump again. I have a ton of parts laying around, I need to assemble them, buy more embedded screws, aaaaand!!! that's it. 

It took a lot of time to build the two reducers, but thankfully they work on the first try! Maybe not perfectly yet, but they work. 

Just a few last steps and the robot will come alive in this very, very positive world... I think its first words will be "why me".

First commit that's not at 4 AM... huh.. <Have a good day guys!>

# 2026-07-05: That was a long way

## Milestone
*   **Assembling:** Second axis assembled and tested.
*   **CAD:** Developed encoder holders for the first 3 real axes.

## Current Status
-   **Assembling:** Reducers for the 2nd and 3rd axes are assembled. The 2nd axis was successfully tested with a 10kg load (or 25Nm) and is now fully assembled.
-   **CAD:** Finished the design of the 3 encoder holders for axes 1, 2, and 3.

## Next Steps
-   **Assembling:** Assemble the final axis.
-   **CAD / CNC:** Start developing the 500W CNC module.
-   **Firmware:** Start developing the main control loop and inverse kinematics.
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

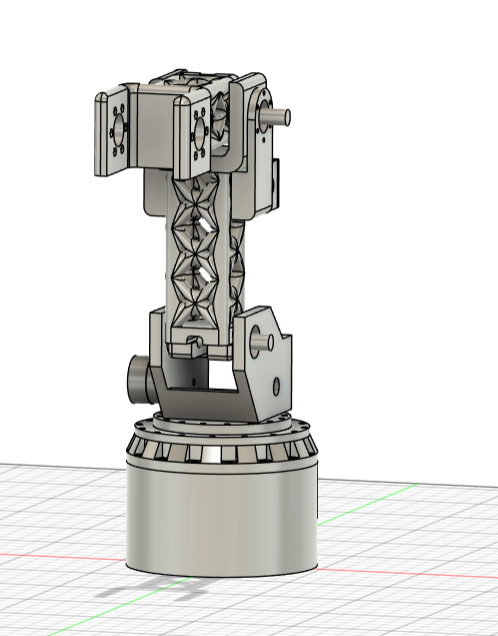
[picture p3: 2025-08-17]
cad/docs/CAD_views/Atlas_v1_pict_2.png

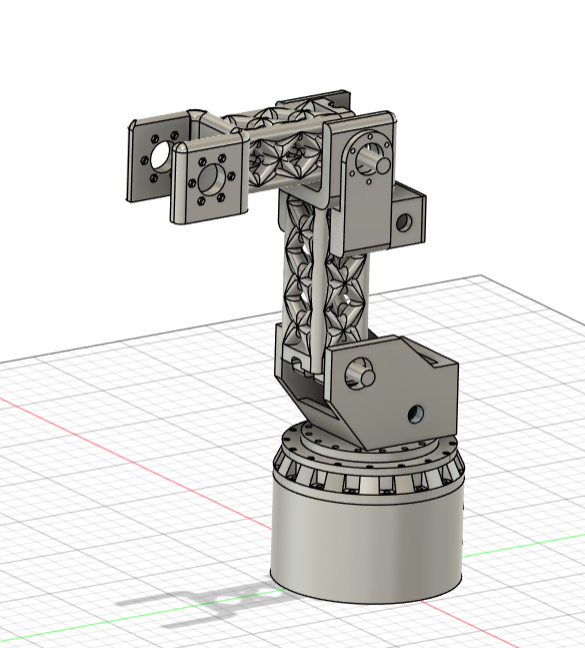
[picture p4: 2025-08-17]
cad/docs/CAD_views/Atlas_v1_pict_1.png

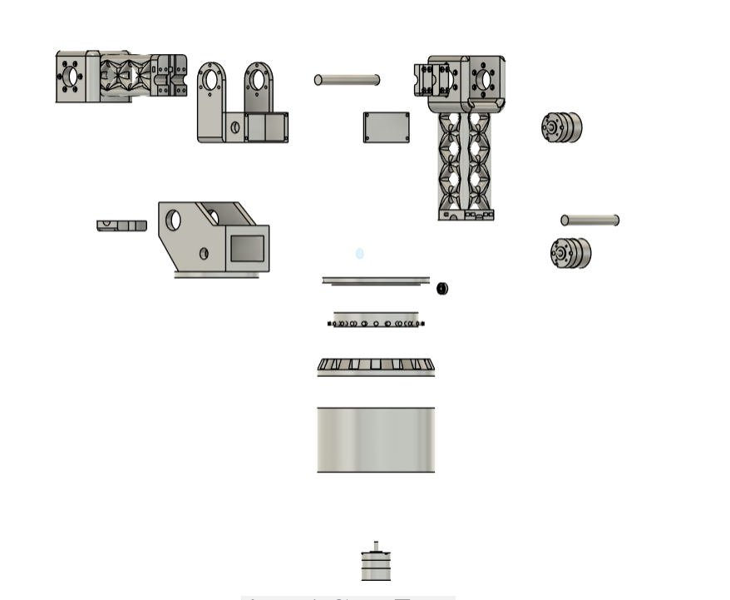
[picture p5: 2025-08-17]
cad/docs/Exploded_views/Pict_3.png

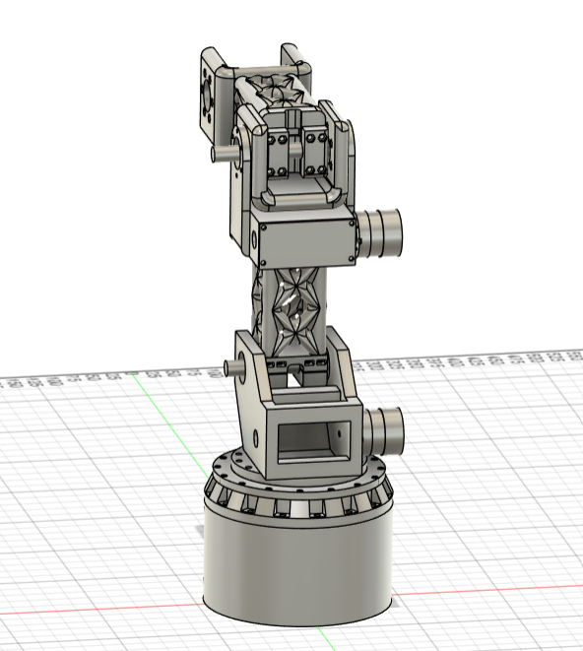
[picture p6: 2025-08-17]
cad/docs/CAD_views/Atlas_v1_pict_5.png

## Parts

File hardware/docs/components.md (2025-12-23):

# Project Components Bible

This document contains a curated list of all components used in the project, with technical specifications and the reasoning behind each choice.

---

# Axis Channel Blade

This section details all components for the modular Axis Channel power blade.

## Power Supply
### DC/DC Converters: TPS54360BDDAR

#### TPS54360BDDAR
- **Type:** Step-Down DC/DC Converter
- **Specs:** 60V max input, 3.5A output
- **Comment:** *It's cheap as a bolt, but it has a 60V input and a 3.5A output, which is just insane. No questions, we're choosing it.*

### LDO (+3.3V): TLV1117-33IDCYR

#### TLV1117-33IDCYR
-   **Type:** Low-Dropout Regulator
-   **Specs:** 3.3V output, 800mA max current, **Stable with Ceramic Capacitors**.
-   **Comment:** *(no comments for legend)*

- **updated: 2025-11-18** BUT LEGEND DONT WORK WITH CERAMIC and when its will be on the plate it will generate many noise. be carefull rly. Just no need to use *

#### LM1117-3.3
-   **Type:** Low-Dropout Regulator
-   **Specs:** 3.3V output, 800mA max current.
-   **Reason for Rejection:** *LEGEND DONT WORK WITH CERAMIC and when its will be on the plate it will generate many noise. be carefull rly. Just no need to use*

### LDO (+5V): LM7805 (DPAK/TO-252)

#### LM7805 (DPAK/TO-252)
- **Type:** Linear Voltage Regulator
- **Specs:** 5V output, 1.5A max current
- **Comment:** *Another legend. It just works.*

### Power Inductors for DC/DC : MWSA0603S-4R7MT

#### MWSA0603S-4R7MT
- **Specs:** 33mΩ 4.7uH 6A 9A ±20%
- **Price:** ~$0.11

#### NPIM74C4R7MTRF
- **Specs:** 4.7uH, 5.5A Saturation Current
- **Price:** ~$0.8

---

## Power Stage & Drivers 
### N-Channel MOSFET: NTMFS3D5N08XT1G

#### NTMFS3D5N08XT1G
- **Type:** Power MOSFET, SMD
- **Specs:** 80V, 3mOhms, Qg = 23nC
- **Comment:** *It's the fastest MOSFET I could find, it's pretty cheap, and has a good thermal package (SuperSO8). Just ideal. The Qg of 23nC is insane!*

#### BSC030N08NS5
- **Type:** Power MOSFET, SMD
- **Specs:** 80V, 3mOhms, Qg = 73nC
- **Comment:** *Just a good and cheap alternative, but not the fastest. If you want, you can use it, you're welcome.*

### Gate Driver: IRS21867S 

#### IRS21867S (Infineon / International Rectifier)
-   **Type:** High and Low Side Driver
-   **Specs:** 600V Max, **4.0A / 4.0A** Peak Current, 3.3V/5V Logic Compatible.
-   **Comment:** *Cheap (0.60$). good specs. over 5k in stock. why not*

#### UCC27282DR (Texas Instruments)
-   **Type:** Half-Bridge Gate Driver
-   **Specs:** 120V Max, 3A Peak Current, 3.3V/5V Logic Compatible, **Input Interlock**.
-   **Reason for Rejection:** *Too expensive.... (on JLCPCB 1$) and only 3A*

#### NCP5106BDR2G (OnSemi)
-   **Type:** Half-Bridge Gate Driver
-   **Specs:** 600V Max, 0.25A/0.5A Peak Current, **100ns internal Dead-Time**.
-   **Reason for Rejection:** *Initially looked like a great cheap and safe option due to the fixed hardware dead-time. However, a deeper look into the datasheet revealed the **output current is too low (0.5A)**. This would lead to slow switching times and massive overheating of the MOSFETs at our target frequencies. A critical flaw.*

#### UCC27201ADDA (Texas Instruments)
-   **Type:** Half-Bridge Gate Driver
-   **Specs:** 20V Max, 3A Peak Current, 3.3V Logic Compatible.
-   **Reason for Rejection:** *This was the first "ideal" candidate. It's powerful and compatible. However, its price is significantly higher (~$1.2+) than comparable or even superior alternatives from other manufacturers.*

#### UCC27282DR-JSM 
-   **Type:** Half-Bridge Gate Driver (Clone)
-   **Specs:** 250V Max, 4A Peak Current, Fixed 250ns Dead-Time.
-   **Reason for Rejection:** *The specs looked good, but this is a clone from a lesser-known Chinese manufacturer (JSMICRO) with a Chinese-only datasheet. I was concerned about long-term availability and reliability. If this driver dies, I don't know where I would find a replacement. So, I just continued my search for a more standard, tier-1 component.*

#### TC4424A (Microchip)
-   **Type:** Dual Low-Side Driver
-   **Specs:** 18V Max, 4.5A Peak Current.
-   **Reason for Rejection:** *Fundamentally unsuitable. This is **not a half-bridge driver**. It cannot drive the high-side MOSFET in our configuration as it lacks a bootstrap circuit. It would be instantly destroyed.*

---

## Measurement & Feedback
### Current Sense Amplifier: INA240A1DR

#### INA240A1DR
- **Type:** Zero-Drift, High-Side/Low-Side Current Sense Amplifier
- **Specs:** Gain = 20 V/V
- **Comment:** *A cheap monster for this job. High CMRR, Zero-Drift, Wide Bandwidth, and a price like rice.*

### Current Sense Shunt Resistor: WSLP25125L000FEA

#### WSLP25125L000FEA
- **Type:** Metal Strip Current Sense Resistor
- **Specs:** 5mOhms, 3W, 1%
- **Comment:** *Just 3 Watts, just cheap, just 1% tolerance. Perfect.*

### ADC & On-Board Logic: STM32G431RBT6

#### STM32G431RBT6
- **Type:** Microcontroller with advanced analog peripherals
- **Specs:** 3x Synchronizable 12-bit ADCs, Cortex-M4 @ 170MHz
- **Comment:** *It's cheap and works like an expensive ADC, but it can also handle logic tasks. The price is like rice. I initially made a mistake and almost ordered the more expensive G474, thinking it was $2. Don't repeat my mistakes, always re-check part names!*

---

## Interface
### RS-485 Transceiver: SN65HVD75DR

#### SN65HVD75DR
- **Type:** 3.3V RS-485/RS-422 Transceiver
- **Specs:** 20 Mbps, 16kV ESD Protection
- **Comment:** *Cheap, popular, can handle my high frequencies, and robust enough for hot-swapping.*

### Input Filter (Encoder): Simple RC Filter

#### Simple RC Filter
- **Type:** Passive Low-Pass Filter
- **Specs:** R=330 Ohm, C=33 pF
- **Comment:** *Chosen because we need to fight very fast high-frequency signals (spikes) and protect the clean square waves from the encoders.*

---

# Motherboard

## Main Connector (Blade Slot): 10018784-10202TLF

#### 10018784-10202TLF
- **Type:** PCIe x8, 98-position, Vertical, Through-Hole Card Edge Connector
- **Comment:** *Spent 4 hours just to find any solution, and using a standard PCIe connector is the only thing I can think of that's cheap, fast, and widely available. I realized 64 pins wasn't enough, so I upgraded to 98.*

---

# Input Board

*(Components for this board will be detailed later)*

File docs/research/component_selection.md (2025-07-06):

That file for components what i need to buy for my robotic manipulator.

**The prices of the components are approximate**

I create few rules for components what i need.
    **1. The components must be cheap**
    **2. The components must be a strong enough for system**
    **3. I can buy any of the components at a regular hardware store.** 

# reducer_cycloid_16:1

 - ## bearing   

        count: 2    size: 17x40x12  name: 6203 2RS    price: 2-3 $
        count: 2    size: 15x35x11  name: 6202 2RS    price: 2-3 $

 - ## Bolt 

        count: 8    name: М6х45                   price: 1> $
        count: 32   name: M4x30                   price: 1> $
        count: 1    name: any small(10>mm) M4     price: 1> $

 - ## Nut

        count: 8    name: M6                     price: 1>  $
        count: 8    name: Round nut M6X20        price: 2-3 $

        count: 1    name: M8                     price: 1>  $  
            comment: its nut for fix input shaft. need be drilled and make M4 carving in drilled wall.

 - ## linear_shaft
         count: 17 
         Diametr: 8 mm 
         lenght: for one reducer 38 mm two: 2 x 38mm + 11mm = 87 mm (11 mm is distance between the reducers)
         price: 2-4 $

# slim_reducer_cycloid_16:1
 - ## bearing   

        count: 2    size: 17x26x5  name: 6803 2RS    price: 1-3 $
        count: 2    size: 15x24x5  name: 6802 2RS    price: 1-3 $

 - ## Bolt 

        count: 8    name: М6х30                   price: 1> $
        count: 32   name: M4x20                   price: 1> $
        count: 1    name: any small(10>mm) M4     price: 1> $

 - ## Nut

        count: 8    name: M6                     price: 1>  $
        count: 8    name: Round nut M6X20        price: 2-3 $

        count: 1    name: M8                     price: 1>  $  
            comment: its nut for fix input shaft. need be drilled and make M4 carving in drilled wall.

 - ## linear_shaft
         count: 17 
         Diametr: 8 mm 
         lenght: for one reducer 27.5 mm two: 2 x 27mm + 11mm = 66 mm (11 mm is distance between the reducers)
         price: 2-4 $

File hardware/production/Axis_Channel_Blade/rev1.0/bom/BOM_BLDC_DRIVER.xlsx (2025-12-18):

Comment | Designator | Footprint | JLCPCB Part#(optional)
4.7uF | C1, C2, C3 | CAP-SMD_1206 | C29823
2.2uF | C8, C9, C32, C33, C48, C49 | CAP-SMD_1206 | C39619
47uF | C14, C34, C35, C51, C10, C50 | СAP-SMD_ECAP D6.3xL7.7mm | C3349
220nF | C11, C12, C13 | CAP-SMD_0805 | C5378
1nF | C15, C16, C17 | CAP-SMD_0805 | C26912
6800pF | C19, C39, C55 | CAP-SMD_0805 | C313092
1uF | C24, C26, C37, C53 | CAP-SMD_0805 | C1712
100nF | C4, C5, C6, C7, C20, C21, C23, C25, C28, C29, C31, C40, C41, C47 | CAP-SMD_0805 | C28233
0.33uF | C36, C52, | CAP-SMD_0805 | C73142
22pF | C45, C46 | CAP-SMD_0805 | C90626
33pF | C22, C30, C42, C44, C56, C57, C58, C59, C60, C61 | CAP-SMD_0805 | C107123
39pF | C18, C38, C54 | CAP-SMD_0805 | C576960
220uF | C_BULK1, C_BULK2, C_BULK3 | СAP-SMD_ECAP 12.5x16.5mm | C487184
10pF | C27, C43 | CAP-SMD_0805 | C344177
Schottky Diod | D1, D5, D6, D9, D10, D11 | SMB | C65011
VRWM=54V VBR=60V | D7 | SMB | C155205
VRWM=13V VBR=16V | D2, D3, D4 | SMB | C113987
600 ohm 100Mhz | FB1, FB2, FB3, FB4, FB5, FB6 | SMD_0805 | C21286
4.7uH | L1, L2, L3, | SMD,7x6.6mm | C408447
135A 80V N-Channel | M1, M2, M3, M4, M5, M6 | SO-8FL | C145537
Shunt 5mOhm 5% | R22, R23, R24 | RES-SMD_2512 3W | C393074
10ohm 5% | R9, R10, R11, R12, R13, R14 | RES-SMD_0805 | C17415
20ohm 5% | R1, R2, R3 | RES-SMD_0805 | C17544
120 Ohm 1% | R25, R26, R34, R35, R48, R49, R50, R51, R52, R53 | RES-SMD_0805 | C17437
330 ohm 1% | R42, R43, R44, R45, R46, R47 | RES-SMD_0805 | C17630
100 kohm 1% | R4, R5, R6, R19, R20, R21 | RES-SMD_0805 | C96346
10.2 kohm 1% | R18, R28, R33, R41 | RES-SMD_0805 | C17402
13 kohm 1% | R17, R32, R40 | RES-SMD_0805 | C17455
53,6 kohm 1% | R29 | RES-SMD_0805 | C21398
84.5 kohm 1% | R15, R30, R38 | RES-SMD_0805 | C17842
91 kohm 1% | R37 | RES-SMD_0805 | C17866
140 kohm 1% | R8, R16, R31, R39 | RES-SMD_0805 | C17460
523kohm 1% | R7, R27, R36 | RES-SMD_0805 | C17742
TPS54360BDDAR | U1, U6, U10 | SOIC-8-EP | C524806
IRS21867STRPBF | U2, U3, U4 | SO-8 | C52290
INA240A1DR | U5, U9 | SOIC-8 | C2060769
TLV1117-33 | U7 | SOT-223-4 | C37359
STM32G431RBT6 | U8 | LQFP-64(10x10) | C431633
LM7805 | U11 | TO-263-3 | C507146
SN65HVD75DR | U12, U13, U14, U15, U16, U17 | SOIC-8 | C57928
18pF 60Ω 8MHz | Y1 | HC-49S-SMD | C312598
VRWM=12V VBR=13.3V | D8 | SMB | C111091

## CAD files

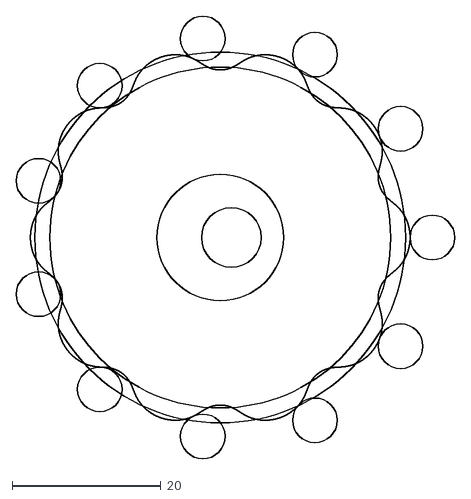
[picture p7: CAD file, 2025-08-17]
cad/docs/drawings/10_to_1_cycloid.dxf
58.9 x 59.5

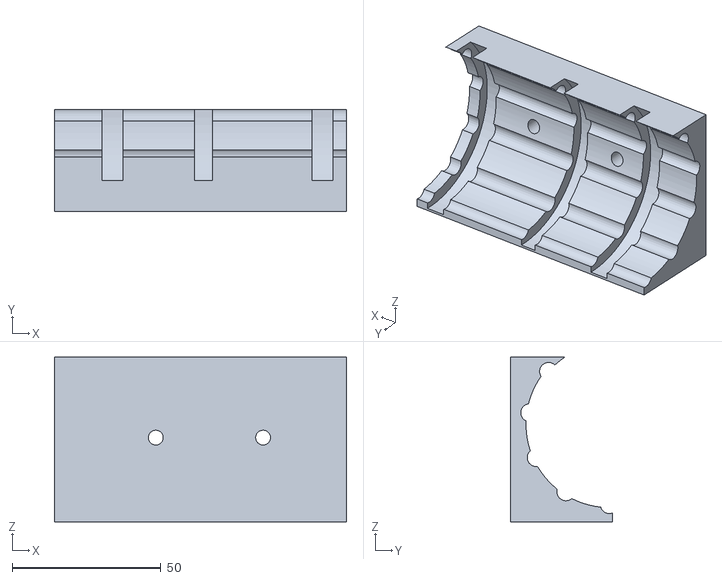
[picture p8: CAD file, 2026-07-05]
cad/manufacturing/stl/Actuator_module/reducer_holder.stl
98.0 x 34.2 x 55.3

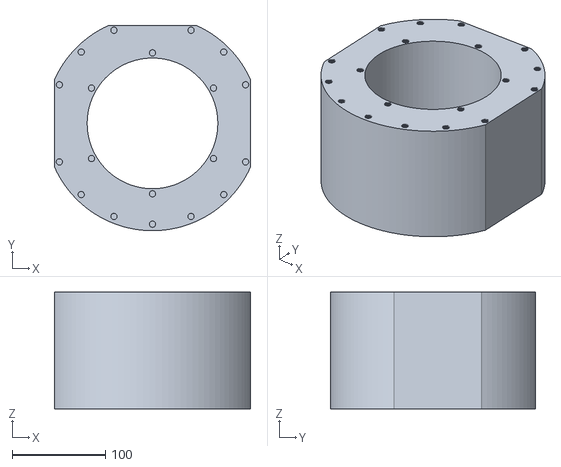
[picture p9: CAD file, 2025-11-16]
cad/manufacturing/stl/Base/Base_V_1_2_.stl
210.0 x 219.9 x 125.0

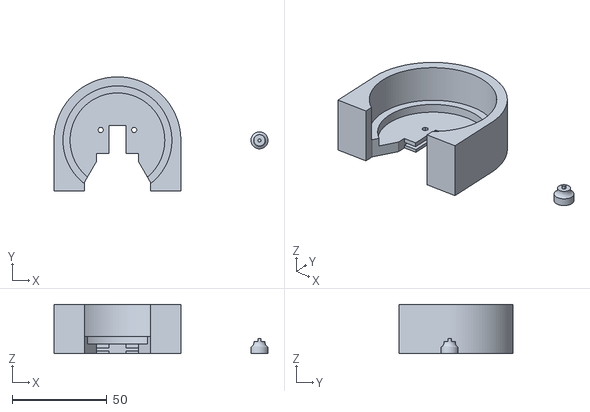
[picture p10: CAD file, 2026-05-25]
cad/manufacturing/stl/hat_for_motor/hat_for_motor_v1.5.stl
113.0 x 60.3 x 26.0

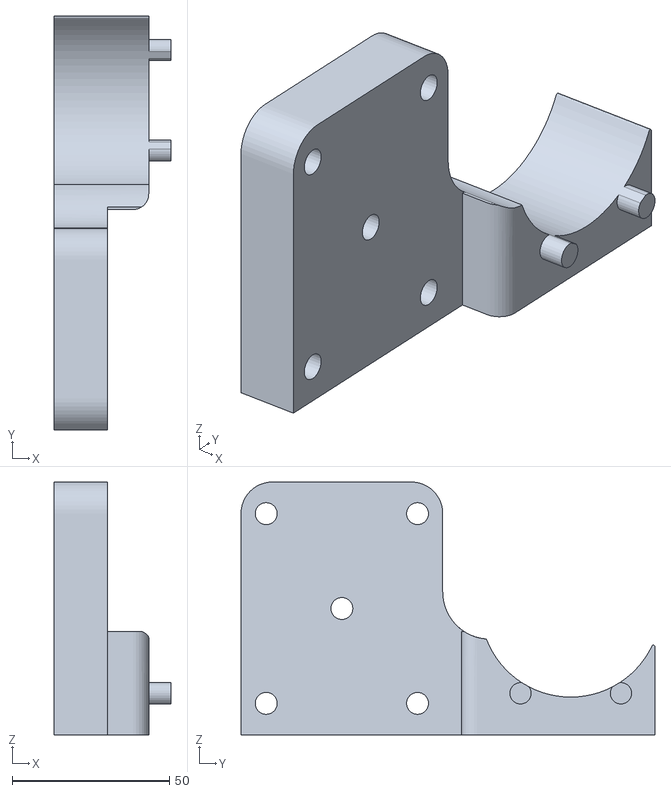
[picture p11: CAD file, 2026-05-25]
cad/manufacturing/stl/motor_holder/motor_holder.stl
37.1 x 131.8 x 80.6

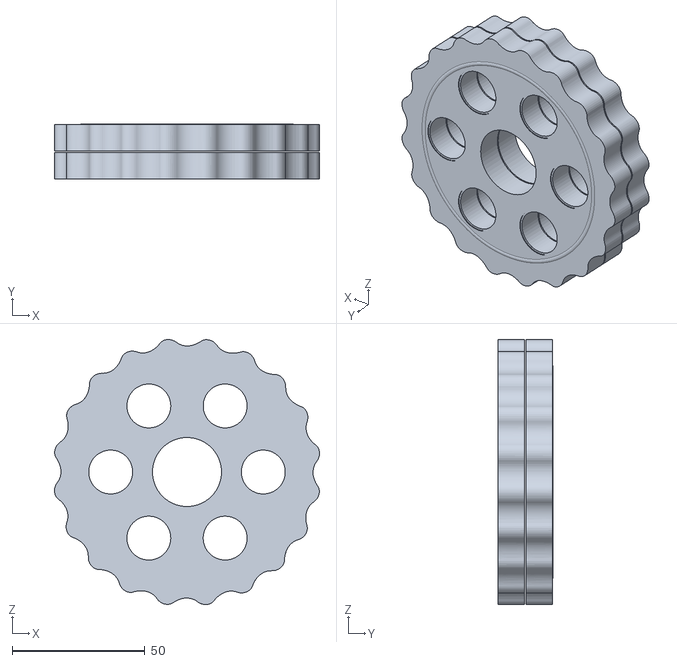
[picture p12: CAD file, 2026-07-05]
cad/manufacturing/stl/Reducers/20to1/20to1_reducer_v1.4.stl
99.9 x 20.7 x 99.9

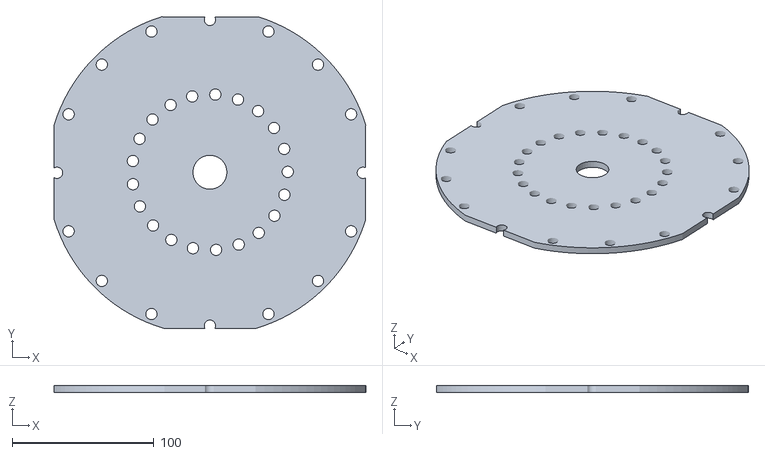
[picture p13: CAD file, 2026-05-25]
cad/manufacturing/stl/Reducers/Adapter/adapter_rotary_reducer_.stl
220.1 x 220.4 x 5.00

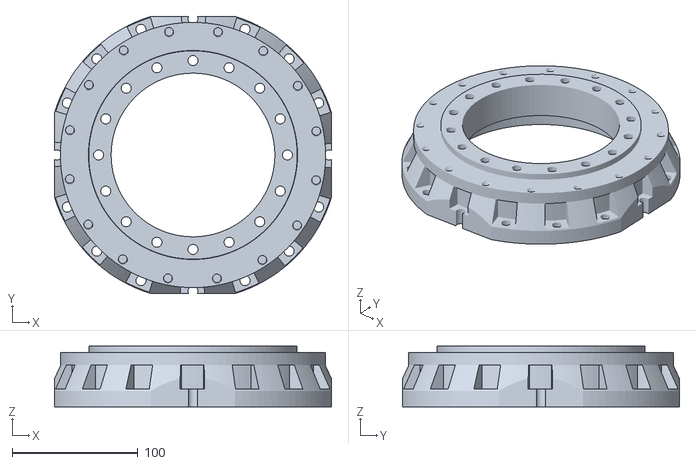
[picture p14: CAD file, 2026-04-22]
cad/manufacturing/stl/Rotary_support/Rotary support_V1.2.stl
220.0 x 220.0 x 48.2

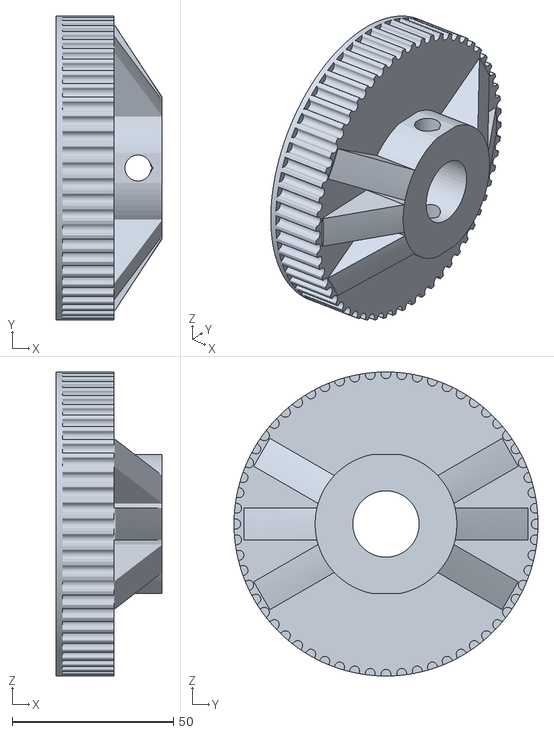
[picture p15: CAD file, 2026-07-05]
cad/manufacturing/stl/Shoulder_Clevis_Mount/wheel_60.stl
33.0 x 94.3 x 94.3

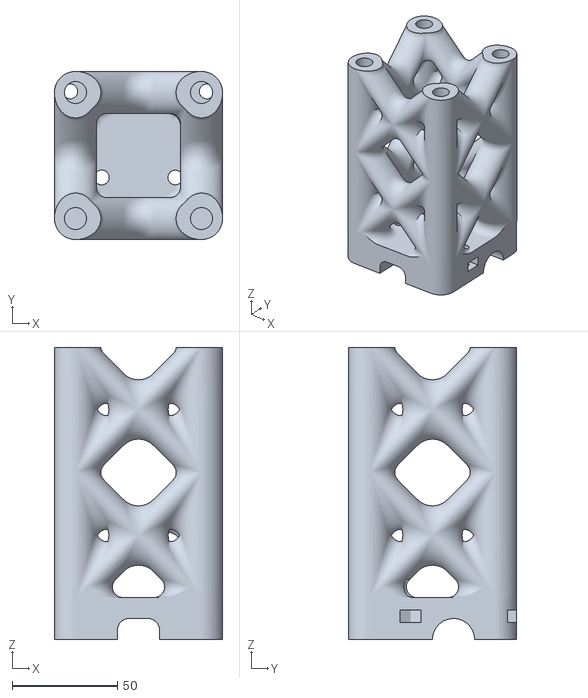
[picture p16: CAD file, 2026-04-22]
cad/manufacturing/stl/Shoulder_module_long/Body_of_1shoulder_module_V1.2_down.stl
80.0 x 80.0 x 139.0

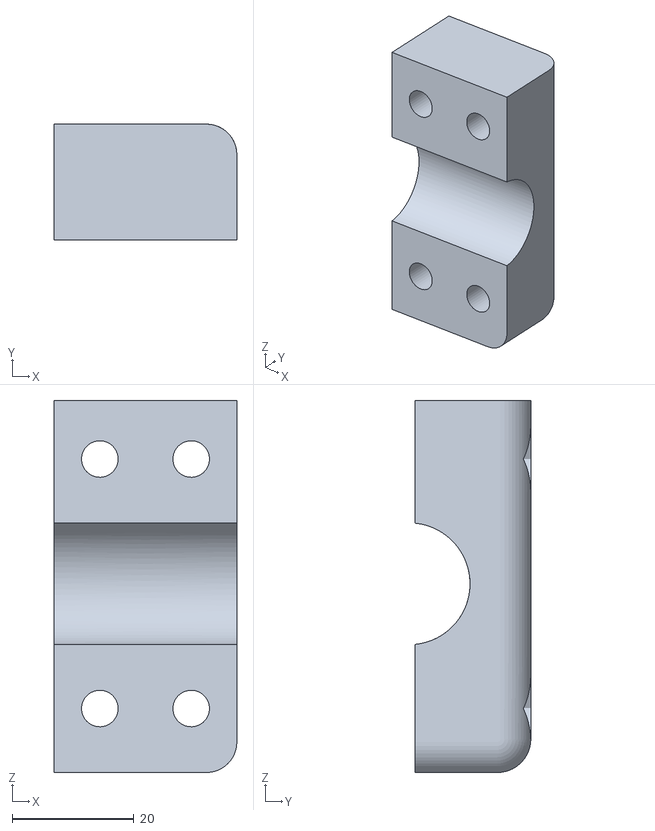
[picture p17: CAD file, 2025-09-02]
cad/manufacturing/stl/Shoulder_module_short/Left_ear.stl
30.0 x 19.0 x 61.1

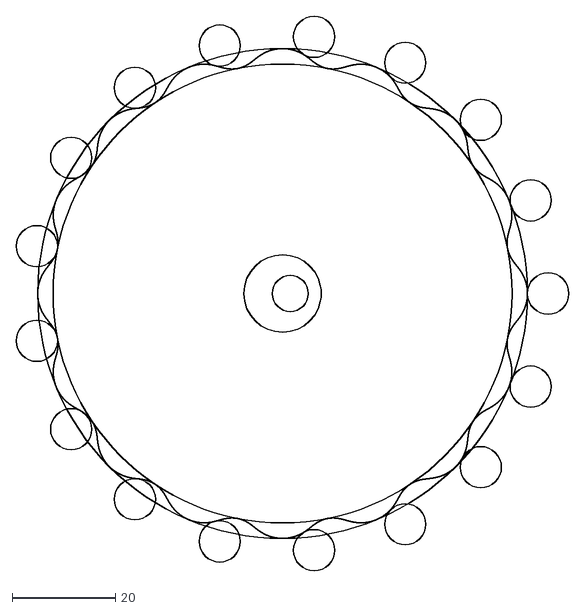
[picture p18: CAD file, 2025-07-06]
cad/docs/drawings/cycloid_16.dxf
107.1 x 107.6

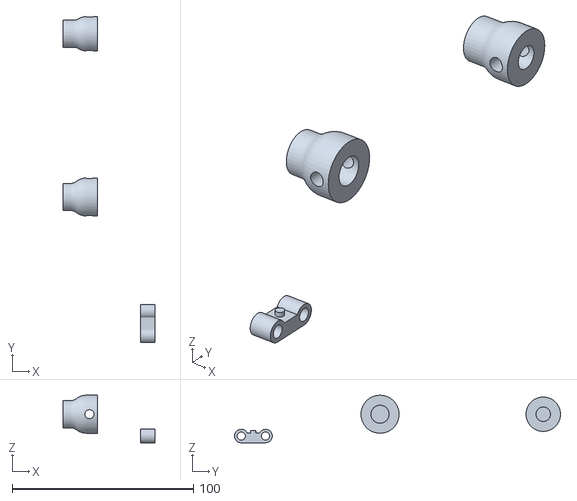
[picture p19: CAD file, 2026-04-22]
cad/manufacturing/stl/Actuator_module/Actuator_module_part.stl
50.5 x 179.7 x 26.3

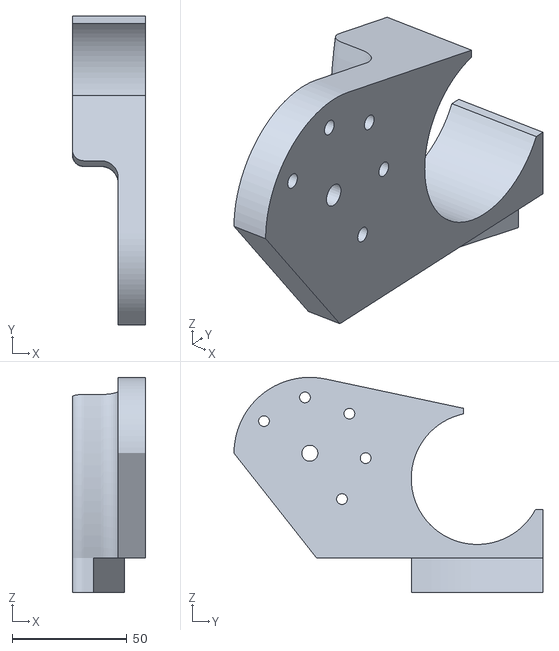
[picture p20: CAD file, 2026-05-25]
cad/manufacturing/stl/motor_holder/motor_holder_clevis.stl
32.0 x 134.8 x 93.9

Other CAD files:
cad/manufacturing/stl/Reducers/20to1/final_20_1_fastdisk_1.1.stl
cad/manufacturing/stl/Reducers/Adapter/adapter_rtry_sprt_clevis.stl
cad/manufacturing/stl/Shoulder_Clevis_Mount/stator_holder.stl
cad/manufacturing/stl/Shoulder_module_long/Left_ear_V1.1.stl
cad/docs/drawings/cycloid_16_revers.dxf
cad/manufacturing/stl/Actuator_module/Actuator_module_V1.1.stl
cad/manufacturing/stl/Reducers/Adapter/adapter_V1.1_8mm.stl
cad/manufacturing/stl/Reducers/Adapter/adapter_V1.stl
cad/manufacturing/stl/Reducers/Adapter/adapter_rotary_reducer_V1.1.stl
cad/manufacturing/stl/Shoulder_Clevis_Mount/Shoulder_Clevis_Mount_V1.3_.stl
cad/manufacturing/stl/Shoulder_Clevis_Mount/Shoulder_Clevis_Mount_V1.3_part.stl
cad/manufacturing/stl/Shoulder_module_long/Body_of_1shoulder_module_V1.1.stl
cad/manufacturing/stl/Shoulder_module_long/Right_ear_V1.1.stl
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

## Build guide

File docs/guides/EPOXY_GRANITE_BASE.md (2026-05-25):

# DIY Epoxy Granite Robot Base: Casting Guide & Mistakes

## 1. Introduction & Philosophy

This guide covers the process of casting a heavy (around 55 kg) epoxy granite base for a robotic manipulator. The core philosophy here is mass, vibration dampening, and using accessible materials. 

This is a very dirty, physical process. I did it outside, and you should too (or at least in a very well-ventilated area). I made some mistakes along the way, so this guide includes not just what to do, but what *not* to do, based on my actual build. 

If you have patience and don't mind getting your hands dirty, you can reproduce this and get an indestructible base that costs a fraction of a cast iron one.

Lets start!

---

## 2. Safety & Preparation

This is not a clean indoor project. 
*   **Work outside:** Epoxy can smell, and the dry powders will get everywhere.
*   **Wear gloves:** I didn't wear gloves at first and mixed the heavy aggregate with a small garden hoe. I ended up with blisters and swollen hands by the end of the day. Epoxy is also extremely hard to wash off your skin. Use thick construction or nitrile gloves.
*   **Tools:** Assume whatever you use for mixing (like my garden hoe or buckets) will be permanently covered in a layer of epoxy. Don't use your favorite tools.

---

## 3. Materials & Proportions

The total weight of my base is around 53-55 kg. The goal is to fill all gaps: large stones form the skeleton, sand fills the gaps between stones, and quartz flour fills the micro-gaps.

**The 55kg Recipe:**
*   **Epoxy Resin with Hardener:** 5 liters/kg (I used tabletop epoxy because it was cheaper and cures slower, giving me 48 hours. Construction epoxy works too).
*   **Gravel/Crushed Stone:** 25 kg. I bought landscaping gravel from a local supply yard. I used 5-20mm, but honestly, I highly recommend using 5-10mm. It will make the mixing process much easier and more uniform.
*   **Quartz Sand:** 15 kg. You can get this at hardware stores (used for sandblasting or pool filters).
*   **Quartz Flour:** 10 kg. Ordered from a marketplace. It is literally like flour and will coat every surface around you.

**Preparation:**
Wash all your gravel to remove dirt. I washed mine and left it outside to dry in the sun (since I wasn't allowed to use the oven). It must be 100% dry before mixing.

---

## 4. The Mold: Design & Dimensions

I originally used a 90-liter plastic tub as the outer shell, but in hindsight, don't buy a tub. The cheapest and best way is to make the entire mold out of PET plastic sheets, tape it together, and just destroy it after the cast.

*   **Material:** Buy PET plastic sheet. I used 0.5mm, and it was barely enough. Ideally, use 1mm thick PET. It will solve a lot of deformation problems.
*   **The Flat Patterns (Unfolding):** If you are building the mold purely out of PET for a base with a 50cm bottom, 27cm top, and 22cm height, you need to cut three specific shapes.
    *   **Bottom Base:** Cut a simple flat circle with a 50 cm diameter. 
    *   **Inner Tube (15 cm diameter):** This is a rectangle. The circumference is 47 cm, plus 5 cm for overlap. Cut a piece 52 cm long and 25 cm high.
    *   **Outer Cone:** A truncated cone unrolls into a "rainbow" shape. Make a DIY compass: take a pushpin with a plastic handle (it sticks into PET really well), tie a piece of string to it, and tie a marker to the other end. Stick the pin in the plastic. Draw the first inner arc at a radius of 33.5 cm. Draw the second outer arc at a radius of 56 cm. Measure exactly 157 cm along that outer arc (this is your 50 cm base circumference), add 8-10 cm for the overlap, and mark your cut lines to the center.
*   **Cutting:** Use garden shears or good scissors. The trick for 0.5mm PET is to take it on a slight bend/angle and slice through it like paper or fabric. It cuts pretty easily this way.
*   **Assembly & Sealing:** Roll the tube and the cone, aligning your overlap marks. Do NOT use silicone sealant. I tried it, it failed completely, and my mold started floating up during the pour. Tape all vertical seams and the bottom joints (where the cone and tube meet the flat base circle) tightly with 2-4 layers of clear or reinforced duct tape. 
*   **Inner Tube Warning:** The pressure of the heavy stones pushed my central PET tube inward, making the center hole much smaller. You must reinforce it. Put something solid and round inside it during the pour.
*   **Release Agent:** I smeared Solidol (grease) all over the inside. Don't rely heavily on grease. The most reliable method is to just line the inside of the mold with a single layer of packing tape. The epoxy will peel right off.

---

## 5. The Embedded Hardware

To mount the robot (or the slewing drive/bearing), you need threads cast into the stone.
*   I bought M6x80mm bolts. 
*   Threaded a ton of regular nuts onto them (about 15 nuts per bolt).
*   Put the bolts through a 3D-printed template.
*   **Smear the bolt threads completely in Solidol/grease** so the epoxy doesn't lock them. (They unscrewed perfectly later).

If your mold deforms (like mine did, losing some height), your template might end up sitting directly on the inner PET tube and not touching the epoxy with its flat surface. Tape the bottom of your template just in case it touches the wet mix.

---

## 6. Mixing Methodology

**CRITICAL: Mix all dry ingredients together first.**
I ended up with about 5 buckets of dry mixed aggregate. If you add epoxy to unmixed powders, the epoxy instantly absorbs into the flour, creating impossible lumps, and you'll be trying to transfer epoxy from these lumps onto dry rocks.

**Do it in 5 batches:**
I did exactly 5 separate mixes to avoid the epoxy boiling and to make it physically manageable.
For each batch:
1. Scoop out a proportional amount of your pre-mixed dry aggregate.
2. Weigh exactly 1 kg of mixed epoxy (resin + hardener) on a scale.
3. Combine and mix thoroughly. 

---

## 7. Pouring, Vibrating, and Leveling

*   **Vibration is key:** For the first few layers, I placed my mold directly on the housing of my bench grinder. The vibration was incredibly strong, and the mixture flowed and leveled out like a pure liquid. 
*   **Tamping:** For the later layers, the mold was too heavy to lift onto the grinder, and I had less epoxy ratio in the mix. I had to pack it down manually with a stick. If you have a concrete vibrator or a vibrating table, use it.
*   **Leveling:** When inserting the bolt template at the top, you need to level it. I placed my phone on top of the template and used a level app. I got it to about 1 degree. Since the robot arm uses software calibration anyway, 1 degree of physical tilt is perfectly fine. 

---

## 8. Demolding & Final Results

Since I used tabletop epoxy, it cured for 48 hours.

Because my tub wasn't perfectly greased, the base got slightly stuck. I had to sharply flip the 90L tub upside down on the street to get the 53+ kg donut to fall out. (If you build the mold entirely out of taped PET sheets as described above, you can just cut the tape and peel the plastic away without this struggle).

Extracting the bolts from the template was a bit tricky. My 15-hour 3D printed template cracked from the tension of a rising bolt when I was unscrewing them, so I just smashed it with a hammer to speed things up. 

Because my central PET tube had collapsed inward, I had to work like a stonemason with a hammer and chisel to clear the hole. I hit it with severe force, and the epoxy granite didn't care at all. The material is brutally strong. The sides and bottom against the PET came out incredibly smooth and void-free.

That's it. Cut the PET, mix dry first, use smaller gravel, and vibrate well. You will get a massive, dead-solid base for your machine.

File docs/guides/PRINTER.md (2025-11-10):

# HSPS Project: Printing Configuration & Replication Guide

## 1. Introduction & Philosophy

This guide provides the exact slicer settings and printing methodology used to create the strong, dimensionally accurate mechanical parts for the HSPS Robotic Manipulator.

The core philosophy is **Strength and Accuracy over Speed**. The goal is not to print fast, but to produce engineering-grade components. Please keep in mind that this is my personal, tested configuration; for your specific printer and filament, some values might need adjustment.

I encourage you to use these settings as a strong starting point. I've tested them, and they produce truly strong parts. It's an interesting and straightforward process, and you can do it too! All you need is time and filament. (I use cheap filament, around $5-6 per kg, so I believe anyone with a 3D printer can afford to experiment and succeed :>)

After some time, I might update this file with new findings, but for now, I consider these settings final and will be printing all core components with them.

I bet anyone can repeat this, because if I could do it (with almost no prior printing experience), you can too!

Lets start!
---

## 2. Hardware & Software Baseline

*   **Printer Model:** Creality Ender 3 v3 SE (Stock)
*   **Nozzle:** Standard Brass 0.4mm
*   **Slicer:** OrcaSlicer (This guide is based on Version 2.3.0)

---

## 3. CRITICAL Pre-Print Ritual: Filament Preparation

This is the most important step. PETG is extremely hygroscopic.
*   **Action:** **ALWAYS dry your PETG filament** before any critical print (65°C for 6-8 hours is recommended).

---

## 4. OrcaSlicer Configuration: Step-by-Step

To replicate the setup, create a new set of profiles and input the following parameters precisely.

### 4.1. Printer Profile (`Creality Ender-3 V3 SE 0.4 nozzle`)

#### Extruder 1 Tab:
*   **Retraction -> Length:** `0.8 mm`
*   **Retraction -> Retraction Speed:** `35 mm/s`
*   **Z Hop -> Z hop when retracting:** `0.3 mm`
*   **Z Hop -> Z hop type:** `Spiral`

### 4.2. Filament Profile (`PETG1`)

#### Filament Tab:
*   **Flow Ratio:** `0.96` (or your calibrated value)
*   **Pressure advance (PA):** `0.05` (or your calibrated value)
*   **Temperature -> Nozzle -> First layer:** `250 °C`
*   **Temperature -> Nozzle -> Other layers:** `245 °C`
*   **Temperature -> Bed -> First layer:** `85 °C`
*   **Temperature -> Bed -> Other layers:** `75 °C`
*   **Max volumetric speed:** `9 mm³/s`

#### Cooling Tab:
*   **Keep fan always on:** `Enabled`
*   **Fan Speed -> Min fan speed:** `30 %`
*   **Fan Speed -> Max fan speed:** `30 %`
*   **Slow down for better layer cooling:** `Enabled`
    *   **Slow down if layer print time is below:** `15 s`
    *   **Min print speed:** `20 mm/s`
*   **Overhang Fan Speed -> Fan speed for overhangs:** `40 %`

### 4.3. Process Profile (`PETG_STRENGTH`)

#### Quality Tab:
*   **Layer height:** `0.2 mm`
*   **Initial layer height:** `0.2 mm`
*   **Extrusion width -> Outer wall:** `0.42 mm`
*   **Extrusion width -> Inner wall:** `0.45 mm`
*   **Extrusion width -> Infill:** `0.45 mm`
*   **Seam -> Seam position:** `Random`
*   **Wall generator:** `Arachne`
*   **Wall generator -> Wall transition threshold angle:** `50 °` 
*   **Wall generator -> Number of wall transitions:** `4` or `5`
*   **Wall generator -> Minimal perimeter width:** `25 %`
*   **Perimeters -> Wall sequence:** `Inner/Outer/Inner`

#### Strength Tab:
*   **Wall loops:** `5`
*   **Top shell layers:** `5`
*   **Bottom shell layers:** `5`
*   **Sparse infill density:** `100 %`
*   **Sparse infill pattern:** `Rectilinear`
*   **Infill/Perimeter Overlap:** `30 %`
*   **Infill after perimeters:** `Disabled` 

#### Speed Tab:

*   **First layer:** `20 mm/s`
*   **First layer infill:** `20 mm/s`
*   **Initial layer travel speed:** `50 mm/s`
*   **Number of slow layers:** `3`

*   **Outer wall:** `35 mm/s`
*   **Inner wall:** `45 mm/s`
*   **Sparse infill:** `50 mm/s`
*   **Internal solid infill:** `50 mm/s`
*   **Support interface:** `50 mm/s`
*   **Bridge(E|I):** `30 mm/s`

*   **Travel:** `50 mm/s`

#### Support:

*   **Enable support:** `+`
*   **Type:** `Tree(auto)`
*   **Style:** `Organic`

*   **Top Z distance:** `0.225 mm`
*   **Bottom Z distance:** `0.225 mm`
*   **Base pattern:** `Lightning`
*   **Base pattern spacing:** `1 mm`

*   **Tree support branch diameter:** `7 mm`

---

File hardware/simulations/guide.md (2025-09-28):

# GUIDE.md

Simulations are easy but have some strange things, like how to add new components. Here's how to do it.

# How to make a simulation

1.  **Clone my repo -^- and just use all my stuff, or...**

2.  Download `LTspice` and open it up.

3.  Download SPICE models from `ti.com` or a similar site.

    *   Just search for your component on their site.

    *   Find the **"Design & development"** or **"Design tools & simulation"** tab.

    *   You need to find the **Unencrypted PSpice Transient Model**. ~~(trans model)~~.

    *   After downloading the `.zip`, find the `YOUR_COMPONENT.lib` file inside.

4.  Now you have a `.lib` file with the model. **Open this `.lib` file with LTspice.**

5.  You'll see a scary file with many scary words. Scroll down until you find the line starting with:
    `**.SUBCKT .... ..... .....**`
    *   *For example, the gate driver's line looks like this:*
        `.SUBCKT UCC27201_TRANS HI VDD LI HB HO HS LO VSS`

6.  **Right-click on this `.SUBCKT` line** and choose **`Create Symbol`**. A window will pop up, just say `Yes`.

7.  Last step is just save this component to /Documents/LTspice/.. and now u have component in LTspice!

8.  Now you can run the simulation! You're great :)

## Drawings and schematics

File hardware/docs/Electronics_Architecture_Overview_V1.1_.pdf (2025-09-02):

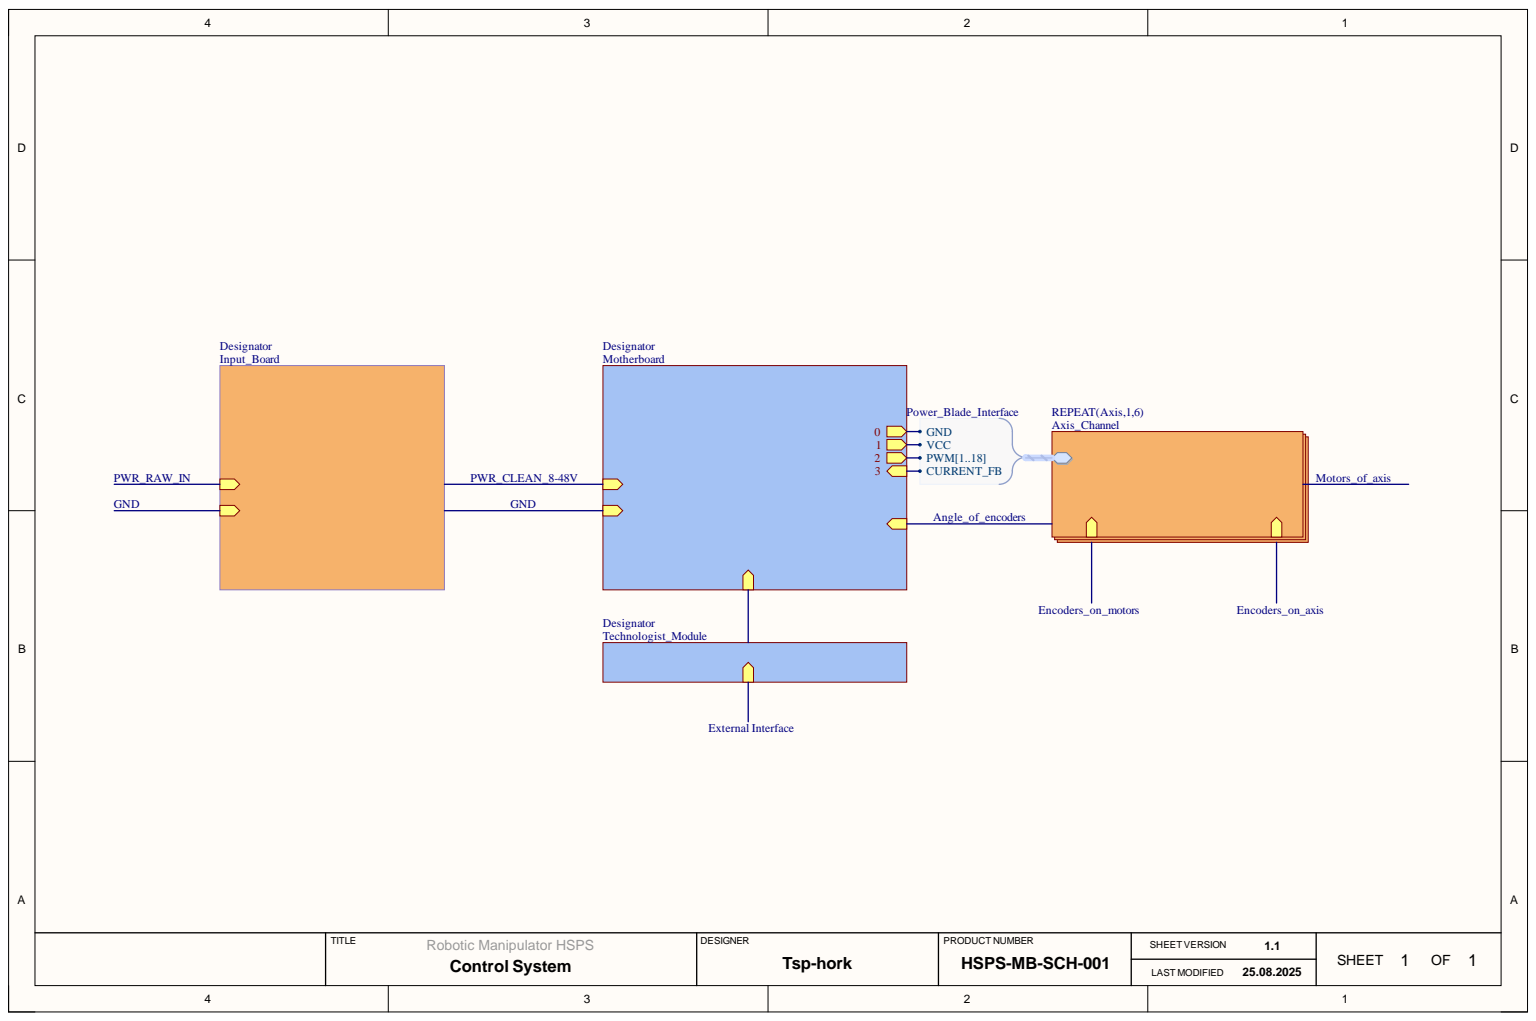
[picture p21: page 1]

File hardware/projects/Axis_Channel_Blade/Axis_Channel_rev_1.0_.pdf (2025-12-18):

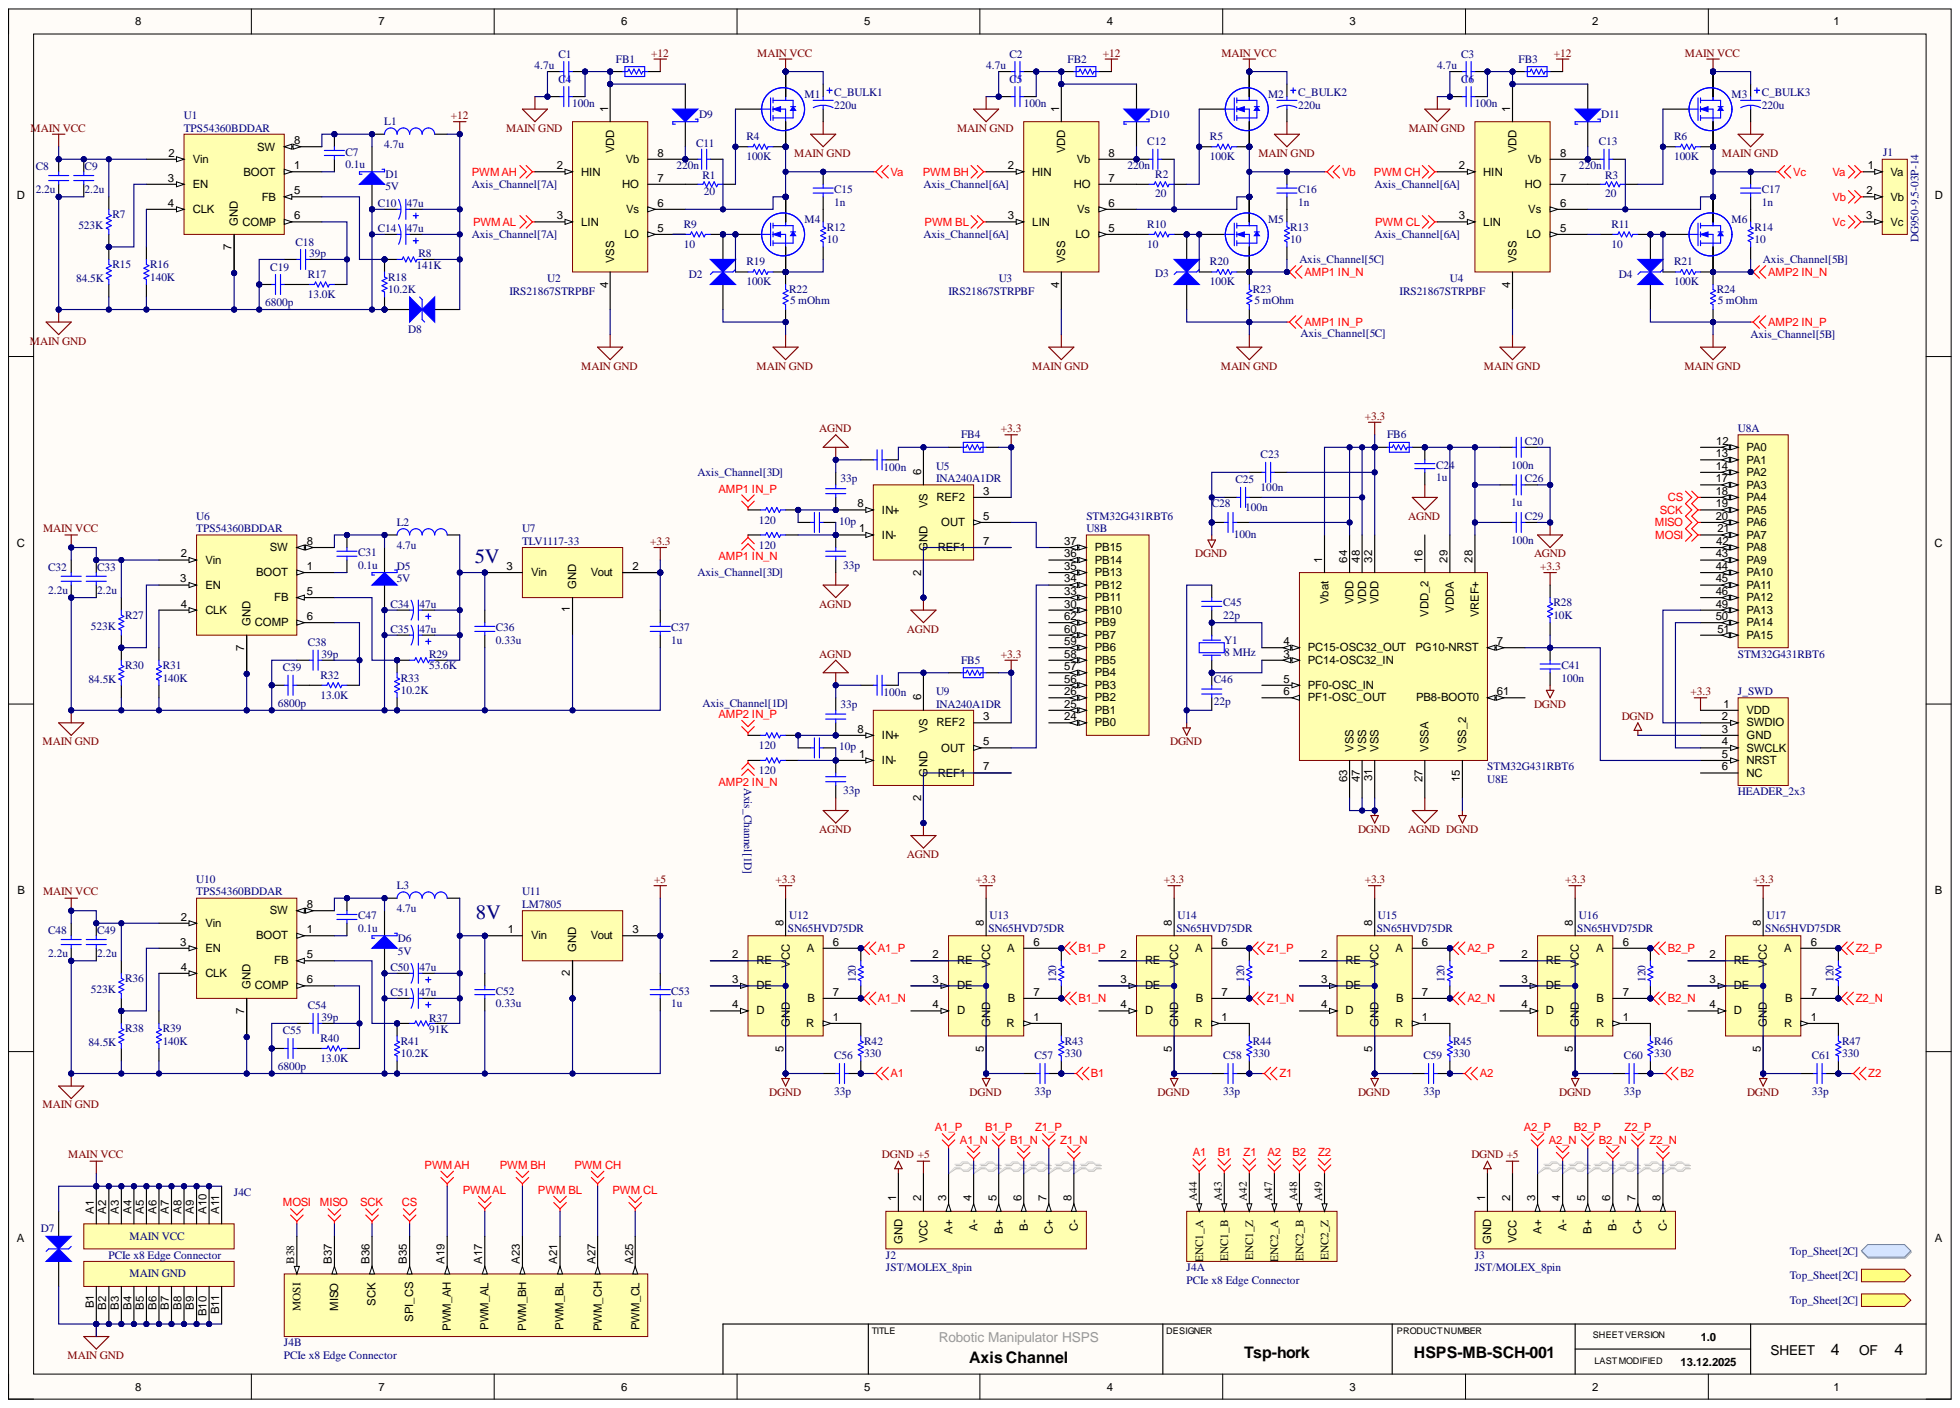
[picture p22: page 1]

VSS 31 VDD 32 VSS 47 VDD 48

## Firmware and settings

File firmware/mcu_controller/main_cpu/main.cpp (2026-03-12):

#include "stm32h7xx.h"
#include "4_driver/stm32h7a3zit6_Q/hw_impl.h"

// These functions are implemented in C source files, so they need
// extern "C" linkage when called from a C++ translation unit.
extern "C" void hw_binding_init(void);  // Initializes all MCU peripherals (rcc, gpio, tim6, spi)
extern "C" void foc_init(void);         // Initializes FOC PI controllers and current references

int main(void) {
    // Set the vector table address to the start of Flash.
    // Required when using a bootloader or when the default VTOR doesn't
    // point to the application's vector table.
    SCB->VTOR = 0x08000000;

    // Initialize all hardware peripherals in the correct dependency order:
    //   rcc_init()       → clock tree (280 MHz)
    //   gpio_init()      → diagnostic LED pins
    //   tim6_init()      → microsecond delay timer
    //   spi_slave_init() → SPI3 + DMA + EXTI4 interrupt
    hw_binding_init();

    // Initialize the FOC current-loop PI controllers (zero integrators, set gains)
    foc_init();

    // Enable global interrupts — the EXTI4 ISR will now fire on every
    // SPI CS edge from the FPGA (~20 kHz), running the entire FOC pipeline.
    __enable_irq();

    // Main loop: all real-time work happens inside EXTI4_IRQHandler.
    // The CPU sleeps between interrupts to save power; WFI (Wait For Interrupt)
    // halts the core until the next interrupt arrives.
    while (1) {
        __WFI();  // Sleep until the next EXTI4 (or any other) interrupt
    }
}

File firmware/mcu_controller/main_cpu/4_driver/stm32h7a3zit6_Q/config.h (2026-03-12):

#ifndef CONFIG_H
#define CONFIG_H

// ============================================================
// Operating mode selection (compile-time)
//   0 = Open-loop rotation test (no encoder feedback)
//   1 = Encoder readback test (motor disabled)
//   2 = Static d-axis alignment (calibrate electrical offset)
//   3 = Align → closed-loop FOC (single axis, with calibrated offset)
//   4 = Full closed-loop FOC (all axes, production mode)
// ============================================================
#define RUN_MODE  3

// ============================================================
// System parameters
// ============================================================
#define AXIS_COUNT      3       // Number of motor axes in the system
#define PWM_PERIOD      1350    // PWM counter ceiling (27 MHz / 20 kHz = 1350)

// ============================================================
// Motor parameters
// ============================================================
#define POLE_PAIRS      2       // Number of electrical pole pairs in the motor
#define ENCODER_CPR     2048    // Encoder counts per mechanical revolution (after X4 decoding)

// ============================================================
// ADC / current sensing
// ============================================================
#define CURRENT_SCALE   0.5f    // Conversion factor: ADC counts → amperes
#define CURRENT_OFFSET  2048    // ADC zero-current reading (mid-scale for 12-bit ADC)

// ============================================================
// Calibration and test constants
// ============================================================
#define ELECTRICAL_OFFSET  0.0f     // Electrical angle offset in radians (for mode 4)
#define TEST_IQ_REF        0.12f    // q-axis current reference for mode 3 testing (amps)
#define ALIGN_TIME         3000     // Alignment duration in packets (~3000 / 20 kHz ≈ 150 ms)
#define ALIGN_AMPLITUDE    0.16f    // Voltage amplitude during alignment phase (normalized)

// ============================================================
// Math constants
// ============================================================
#define PI_F            3.14159265358979f    // π as single-precision float
#define TWO_PI_F        6.28318530717959f    // 2π as single-precision float

#endif

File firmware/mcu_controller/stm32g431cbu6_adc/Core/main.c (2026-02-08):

#include "stm32g4xx.h"
#include "rcc.h"
#include "adc.h"
#include "spi.h"

int main(void) {

    //Init

    RCC_Init(); // 170 MHz
    ADC_Init(); // 42 MHz
    SPI_Init(); // Slave

    // ADC and SPI (u never know what)

    ADC_Start();
    SPI_Start();

    while (1) {
        __asm("wfi"); 
    }
}

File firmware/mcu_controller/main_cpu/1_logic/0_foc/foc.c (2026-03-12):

#include "foc.h"
#include "config.h"
#include "pid.h"
#include <math.h>

#define AXIS_MAX 3                      // Maximum number of motor axes supported
#define ONE_OVER_SQRT3  0.57735026919f  // Pre-computed 1/√3, used in Clarke transform

// ============================================================================
// Per-axis PI current controllers for the d-q frame.
// Two controllers per axis: one for the d-axis (flux), one for the q-axis (torque).
// ============================================================================
static pi_controller_t pi_d[AXIS_MAX];  // d-axis (flux) PI controllers
static pi_controller_t pi_q[AXIS_MAX];  // q-axis (torque) PI controllers

// Per-axis current setpoints (references)
static float iq_ref[AXIS_MAX];          // q-axis current reference — set by the outer servo loop
static float id_ref[AXIS_MAX];          // d-axis current reference — always 0 (no field weakening)

// PI controller tuning constants (shared by all axes)
#define FOC_KP    0.5f                  // Proportional gain
#define FOC_KI    0.0004f               // Integral gain (accumulated per call)
#define FOC_LIMIT 1.0f                  // Output saturation limit (normalized ±1.0)

// ============================================================================
// foc_init: initialize all per-axis PI controllers and zero the current references.
// Must be called once at startup before any foc_step() calls.
// ============================================================================
void foc_init(void) {
    for (int i = 0; i < AXIS_MAX; i++) {
        pi_init(&pi_d[i], FOC_KP, FOC_KI, FOC_LIMIT);
        pi_init(&pi_q[i], FOC_KP, FOC_KI, FOC_LIMIT);
        iq_ref[i] = 0.0f;
        id_ref[i] = 0.0f;
    }
}

// ============================================================================
// foc_set_iq_ref: set the q-axis (torque) current reference for a given axis.
// Called by the outer position/velocity servo loop to command motor torque.
// ============================================================================
void foc_set_iq_ref(uint32_t axis, float ref) {
    if (axis < AXIS_MAX) {
        iq_ref[axis] = ref;
    }
}

// ============================================================================
// foc_step: execute one iteration of the Field-Oriented Control algorithm.
//
// Inputs:
//   axis  — motor axis index (0, 1, or 2)
//   i_a   — measured phase-A current (amps, from ADC)
//   i_b   — measured phase-B current (amps, from ADC)
//   angle — electrical rotor angle in radians (from encoder × pole pairs)
//
// Returns:
//   foc_output_t containing v_alpha, v_beta (voltage commands in stationary
//   frame, normalized ±1.0) and i_d, i_q (measured currents in rotating frame,
//   for telemetry/debugging).
//
// Processing pipeline:
//   1. Clarke transform:       (ia, ib) → (iα, iβ)
//   2. Park transform:         (iα, iβ) → (id, iq)   using rotor angle
//   3. PI current regulators:  error → (vd, vq)
//   4. Inverse Park transform: (vd, vq) → (vα, vβ)   back to stationary frame
// ============================================================================
foc_output_t foc_step(uint32_t axis, 
                      float i_a, float i_b, float angle) {
    foc_output_t out = {0};

    if (axis >= AXIS_MAX) return out;  // Guard against invalid axis index

    // ===== Clarke Transform: 3-phase currents → 2-axis stationary frame (αβ) =====
    // Uses the two-sensor variant: ic = -(ia + ib) is implied, not measured.
    float i_alpha = i_a;
    float i_beta  = (i_a + 2.0f * i_b) * ONE_OVER_SQRT3;

    // ===== Park Transform: stationary αβ → rotating dq frame (aligned with rotor flux) =====
    float sin_a = sinf(angle);  // sin(θ_electrical)
    float cos_a = cosf(angle);  // cos(θ_electrical)

    float i_d_real =  i_alpha * cos_a + i_beta * sin_a;   // d-axis current (flux component)
    float i_q_real = -i_alpha * sin_a + i_beta * cos_a;   // q-axis current (torque component)

    // Store measured d/q currents in the output struct for telemetry / debugging
    out.i_d = i_d_real;
    out.i_q = i_q_real;

    // ===== PI Current Regulators =====
    // d-axis: regulate to zero (no field weakening) → minimizes reactive current
    float error_d = id_ref[axis] - i_d_real;  // id_ref is always 0
    // q-axis: regulate to iq_ref set by the outer servo loop → controls torque
    float error_q = iq_ref[axis] - i_q_real;

    float v_d = pi_step(&pi_d[axis], error_d);  // d-axis voltage command
    float v_q = pi_step(&pi_q[axis], error_q);  // q-axis voltage command

    // ===== Inverse Park Transform: rotating dq → stationary αβ =====
    // Converts the voltage commands back to the stationary reference frame
    // so they can be fed into the SVPWM modulator.
    out.v_alpha = v_d * cos_a - v_q * sin_a;
    out.v_beta  = v_d * sin_a + v_q * cos_a;

    return out;
}

// ============================================================================
// foc_calc_svpwm: Space-Vector PWM modulator.
//
// Converts voltage commands in the stationary αβ frame (range ≈ -1..+1) into
// three unsigned PWM timer compare values (0 .. PWM_PERIOD) suitable for the
// FPGA's center-aligned PWM generators.
//
// Algorithm:
//   1. Inverse Clarke: (vα, vβ) → (va, vb, vc)  — balanced 3-phase voltages
//   2. Center-aligned injection: shift all three by the midpoint of min/max
//      to maximize DC bus utilization (equivalent to 3rd-harmonic injection).
//   3. Normalize from (-0.5 … +0.5) to (0 … 1).
//   4. Clip to [0, 1] for safety.
//   5. Scale to integer timer ticks (0 … PWM_PERIOD).
// ============================================================================
#define PWM_PERIOD_F ((float)PWM_PERIOD)  // PWM counter ceiling as float, for scaling
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

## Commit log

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2025-07-06 docs(cad/drawings): add drawn for cycloid reducer 16:1; docs(component_selection): add description for file and list of components for reducers
    [cycloid_16.dxf, cycloid_16_revers.dxf]
2025-08-17 feat(cad): Add initial 6-axis mechanical assembly and restructure directory
    This is a major milestone commit that introduces the first complete mechanical structure for the robot, designed as a modular platform.
    Key additions:
    - **Structural Components:**
    - Base and custom Slewing Bearing (Axis 1).
    - Shoulder Joint assembly (Axis 2).
    - Elbow Joint assembly (Axis 3).
    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
    [10_to_1_60x60x35_cycloidal.f3d, 10_to_1_cycloid.dxf, 16_to_1_128x128x46_cycloid.f3d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]
2025-08-24 feat: Begin electronics design and add first working mechanical part
    This commit marks the start of Stage II: Electronics Development.
    - **docs:** Added the top-level electronics architecture overview (Top_Sheet.pdf) to the hardware documentation.
    - **docs:**Update the README for the hardware/electronics design.
    - **cad:** Added the working, validated CAD and STL file for the 10:1 cycloidal reducer.
    The reducer model has been corrected after initial printing tests revealed a kinematic conflict. The output disc holes have been enlarged based on the new formula for balanced drives (Pin_Dia + 4*e), and the drive is now confirmed to be working.
    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
    [10_to_1_60x60x35_cycloidal.f3d, 10_to_1_60x60x35_cycloidal_V1.2.f3d, 10_to_1_60x60x35_cycloidal_V1.2.stl]
2025-09-02 docs: update DEVELOPMENT_LOG and structure of hardware
    * update DEVELOPMENT_LOG
    * add architecture of power blade
    * update structure of hardware
    * add stl files to manufacturing for short shoulder module
    [Axis_Channel.SchDoc, Body_of_2shoulder_module.stl, Left_ear.stl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]
2025-09-07 feat(hardware): Complete 90% of Power Blade schematic design
    - Completed the component selection for the axis channel, including datasheets.
    - Created the initial schematic for the Power Blade module, reaching 90% completion.
    - Added new documentation for the hardware architecture and component choices.
    [Axis_Channel.SchDoc]
2025-09-14 docs: update DEV_LOG and README
    just described what i did on this weekend, is was not small but not on plan :/
    [Axis_Channel.SchDoc]
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2025-09-16 feat: add schematics for power blade components
    * Update DEV_LOG
    * Add schematics to hardware/libraries/... symbols and footprint
    * Change MC for ADC (can read in components.md)
    [Axis_Channel.SchDoc]
2025-09-22 feat(hardware): complete principle schematic and start simulations/prints
    * Completed the principle schematic.
    * Began simulations (INA240 in LTspice).
    * Started printing second part of shoulder module and successfully assembled it on the shaft.
    * Resolved connector choice: moved from mezzanine to a PCI connector due to cost/compatibility.
    [Axis_Channel.SchDoc, TPS54360_AVG.DSN, TPS54360_TRANS.DSN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]
2025-09-25 feat: Made 4 simulations for INA240 amplifier
    * Add all spice schematics for axis channel blade
    * Create directory `simulatons`
    * Made 4 simulations for `INA240` amplifier.
    * Made telegram channel
    [Axis_Channel.SchDoc]
2025-09-28 feat(hardware): Finalize Axis Channel schematic and simulation verification
    Completed the final, detailed schematics for all modules of the Axis Channel blade, including:
    - Multi-stage power supply (DC/DC + LDO)
    - Three-phase inverter with gate drivers and protection circuits
    - Dual encoder interface with RS-485 receivers and filtering
    - On-board ADC-controller (STM32G4) with full core device support
    Performed SPICE simulations for all critical analog and power stages in LTspice. The DC/DC converters and the current sense amplifier circuits have been fully verified under various conditions.
    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
    [10_to_1_60x60x35_cycloidal_V1.2.f3d, 10_to_1_60x60x35_cycloidal_V1.2.stl, 10_to_1_64x64x35_cycloidal_V1.3.f3d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]
2025-10-06 feat(hardware): Finalize component libraries and initialize PCB layout
    This commit concludes the component creation and schematic finalization phase for the Axis Channel blade.
    - A complete, custom Altium library (.SchLib, .PcbLib) has been created for every component required for the Axis Channel design.
    - All default components in the schematic have been replaced with these verified, custom library parts.
    - The PCB document (`Axis_Channel_Blade.PcbDoc`) has been created and initialized:
    - Board outline is defined as 100x100mm.
    - The 4-layer stackup (Top/GND/PWR/Bottom) is configured.
    - All components from the final schematic have been successfully imported.
    Minor verification simul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
    [Axis_Channel.SchDoc, Axis_Channel_Blade.PcbDoc]
2025-10-13 fix(hardware): Correct DC/DC schematic and complete simulation
    This commit addresses a critical design flaw found in the DC/DC converter circuitry.
    - The schematics for the 12V, 8V, and 5V converters were successfully simulated in LTspice.
    - A major issue with the feedback (COMP) and output stages was identified and corrected.
    - The updated, validated schematic for theAxis Channelhas been committed.
    - Also includes updates to the printer support settings after successful test prints.
    The project is now unblocked and ready to proceed with the PCB layout phase.
    [Axis_Channel.SchDoc]
2025-10-20 feat(hardware): Completed the placement of all main power components
    * Completed the placement of all main power components
    * Started printing the long upper part of the shoulder module.
    [Axis_Channel.SchDoc, Axis_Channel_Blade.PcbDoc, Generic_Axis_Channel_Blade.PcbDoc]
2025-10-21 refactor(hardware): Optimize power stage placement to minimize gate drive loops
    Completed a major refactoring of the Axis Channel's power stage component placement.
    The primary objective was to minimize the gate drive loop inductance for both high-side and low-side MOSFETs. The layout was reworked to bring the UCC27201ADDA gate driver outputs as close as physically possible to the MOSFET gate pins.
    - The trace length for the high-side gate drive path has been reduced from ~10mm to approximately 1.5mm - 1.8mm.
    - This significant reduction will improve switching performance, minimize ringing on the gate, and reduce switching losses, leading to higher overall efficiency and better thermal per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
    [Axis_Channel.SchDoc, Generic_Axis_Channel_Blade.PcbDoc]
2025-10-26 feat(hardware): Complete 90% of Axis Channel component placement
    * Finished placing the RS-485 receivers, the MCU-ADC, and the 5V DC/DC converter.
    * Started printing the long upper part of the shoulder module... again...
    * Tested new hole sizes for the pins in the 10:1 reducer.
    * Dialed in new settings for Orca Slicer.
    [10_to_1_64x64x35_cycloidal_real_V1.5.f3d, 10_to_1_64x64x35_cycloidal_real_V1.5.stl, Generic_Axis_Channel_Blade.PcbDoc]
2025-11-02 feat(hardware): Complete component placement for Axis Channel blade
    * Finished component placement for the Axis Channel blade.
    * Finished printing the long upper part of the shoulder module.
    [Generic_Axis_Channel_Blade.PcbDoc]
2025-11-09 feat(hardware): Complete Top Layer routing and refine component placement
    * Replaced the MCU and its supporting components on the layout.
    * Completed the initial routing for the entire Top Layer of the Axis Channel blade (~50% of total routing).
    [Axis_Channel.SchDoc, Generic_Axis_Channel_Blade.PcbDoc]
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2025-11-16 feat(pcb): added PWR and GND plane
    * Successfully assembled the head-shoulder module.
    * Learned all about vias and planned the layout for the GND and PWR planes.
    * Finally bought the 10mm shafts.
    [Axis_Channel.SchDoc, Base_V_1_2_.stl, Generic_Axis_Channel_Blade.PcbDoc]
2025-11-17 feat(pcb): Complete routing for all signal, analog, and core logic sections
    This commit marks the completion of routing for all low-power and signal-level sections of the Axis Channel PCB. The "quiet" side of the board is now considered feature-complete at the layout stage.
    Key routed subsystems include:
    - The MCU-ADC core (STM32G4) with all support circuitry.
    - The dual current-sense amplifier circuits, routed with matched-length and shielded traces.
    - The dual encoder interface with RS-485 receivers and filtering.
    - The 5V DC/DC power supply and its distribution network.
    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
    [Generic_Axis_Channel_Blade.PcbDoc]
2025-11-18 refactor(hardware): Replace LM1117 with TLV1117 for ceramic capacitor stability
    Replaced the legacy LM1117-3.3 LDO with the modern, pin-compatible TLV1117-33IDCYR.
    **Reasoning:**
    Discovered during the final layout stage that the older LM1117 is unstable with low-ESR ceramic output capacitors, which can lead to severe oscillations and noise on the power rail. The TLV1117 is specifically designed to be stable with ceramic capacitors, has better overall performance (lower dropout, higher PSRR), and ensures the reliability of the sensitive 3.3V analog and digital power domains.
    This change is critical for the stability and performance of the entire Axis Channel blade.
    In parallel, the SPI pin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
    [Axis_Channel.SchDoc, Generic_Axis_Channel_Blade.PcbDoc]
2025-11-23 feat(hardware): Finalize PCB routing and update mechanical base design
    This commit marks the completion of the PCB routing phase for the Axis Channel blade.
    - **PCB:** Fully routed all signals (High-speed, Analog, Power) on all 4 layers. The layout includes optimized power planes, differential pair routing for encoders, and via stitching for thermal management and EMI suppression. Ready for Design Rule Check (DRC) and manufacturing generation (Gerber/BOM).
    - **Mechanical Update:**
    - **Base:** Transitioned from a 3D-printed design to a concrete block anchor. This decision reduces cost, print time, and significantly increases structural rigidity and vibration dampening.
    - **Reducer:** Im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
    [Axis_Channel.SchDoc, Generic_Axis_Channel_Blade.PcbDoc, Rotary support.f3d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]
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2025-12-23 docs(hardware): Update component selections and log mechanical progress
    This commit updates the project documentation to reflect final component decisions and recent progress in mechanical fabrication.
    - **components.md:** Updated the Gate Driver and LDO sections with final, verified part numbers and detailed rejection reasons for alternative components. This concludes the primary component selection research.
    - **Mechanical:** The main slew drive component has been successfully 3D printed after resolving previous warping issues by using a temporary enclosure and new slicer settings.
    The PCB fabrication order is pending final logistics. The upcoming period will be dedicated to intensive f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
2026-01-02 firmware(fpga): FPGA Core & Printer Fix
    - FPGA: Implemented ~80% of core firmware (SystemVerilog).
    - Added system_storage (CSR), pwm_generator (Center-Aligned), deadtime, and quadrature_decoder.
    - Fixed open-collector encoder issue with external pull-ups.
    - CAD/Mfg:
    - Installed new PEI plate.
    - Fixed critical printer toolhead misalignment.
    - Started printing final reducer parts.
    [10_to_1_64x64x35_cycloidal_V1.4.f3d]
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2026-04-22 feat(cad, pcb): verify boards, update reducers and fix architecture docs
    - PCB: All systems tested and functional. Fixed a copper short under a suppressor in the 3rd half-bridge. Updated Gerbers with the fix.
    - CAD: Printed 60t rollers, designed motor holder, and developed a new 20:1 reducer.
    - CAD: Assembled and successfully tested the rotary support.
    - Docs: Restored and fixed architecture.md after accidental deletion.
    - Miscellaneous: Started assembly phase and thesis documentation.
    [10_to_1_64x64x35_cycloidal_V1.5.f3d, 10_to_1_64x64x35_cycloidal_V1.5.stl, 10_to_1_64x64x35_cycloidal_V1.6.f3d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]
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

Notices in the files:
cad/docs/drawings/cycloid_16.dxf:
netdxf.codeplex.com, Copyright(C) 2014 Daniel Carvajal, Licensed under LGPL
